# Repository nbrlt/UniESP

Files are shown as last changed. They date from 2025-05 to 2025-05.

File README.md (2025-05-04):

# UniESP
This is a simple board to control 2 unipolar stepper motors. It is meant to control a telescope mount using OnStepX on the ESP32. 

It relies on an ESP32 dev board with 30 pins and a RP2040 in the form of the Raspberry pico zero from waveshare as the driver logic. 

The code for OnStepX is found here: https://github.com/nbrlt/OnStepX (for now).
## The RP2040
The RP2040 is used to convert the StepDir interface of OnStepX to a 4 pin control for the DRV8932. I used that specific bridge driver to have a current control on the stepper (I could not find any StepDir bridge with proper current control).

The code for the Raspberry pico zero can be found here: [https://github.com/nbrlt/RP2040_Unipolar_StepDir_Driver](https://github.com/nbrlt/RP2040_StepDirToPWM_StepperLogic)

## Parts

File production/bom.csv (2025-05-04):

Designator | Footprint | Quantity | Value | LCSC Part #
C1, C16, C17 | 0402 | 3 | 0.01uF
C10, C4 | CP_Radial_D6.3mm_P2.50mm | 2 | 100uF
C11, C5 | 0402 | 2 | 0.022uF
C12, C15, C6, C9 | 0402 | 4 | 0.01uF
C13, C7 | 0603 | 2 | 0.22uF
C14, C8 | 0603 | 2 | 0.47uF
C2 | 0603 | 1 | 10uF
C3 | CP_Radial_D6.3mm_P2.50mm | 1 | 220uF
D1 | D_SMA | 1 | D | C14996
J1 | PinHeader_1x04_P2.54mm_Vertical | 1 | Power Conn
J2 | JST_NV_B02P-NV_1x02_P5.00mm_Vertical | 1 | 12V Input
J3 | PinHeader_1x05_P2.54mm_Vertical | 1 | RTC conn
J4 | PinSocket_1x10_P2.54mm_Vertical | 1 | Extra conn
J5 | JST_XH_B5B-XH-A_1x05_P2.50mm_Vertical | 1 | Motor2_Output
J6 | RJ45_HALO_HFJ11-x2450HRL_Horizontal | 1 | M2_out
J7 | JST_XH_B5B-XH-A_1x05_P2.50mm_Vertical | 1 | Motor1_Output
J8 | RJ45_HALO_HFJ11-x2450HRL_Horizontal | 1 | M1_out
L1 | L_Changjiang_FNR5040S | 1 | 15uH | C167969
R1 | 0603 | 1 | 10k
R10, R4 | 0603 | 2 | 330k
R11, R5 | 0603 | 2 | 3k
R12, R6 | 0603 | 2 | 4.7k
R13, R7 | 0603 | 2 | 10k
R14, R8 | 0603 | 2 | 27k
R15, R16, R3, R9 | 0603 | 4 | 47k
R2 | 0603 | 1 | 3.3k
RP2040_ZERO1 | WS_Pico_Zero_header | 1 | ~
U1 | TI_SO-PowerPAD-8_ThermalVias | 1 | TPS5430DDA | C9864
U2 | ESP32-DevKitV1 | 1 | ESP32-DevKitV1
U3, U4 | VQFN-24-1EP_4x4mm_P0.5mm_EP2.45x2.45mm_BIGThermalVias | 2 | DRV8932 | C2876703

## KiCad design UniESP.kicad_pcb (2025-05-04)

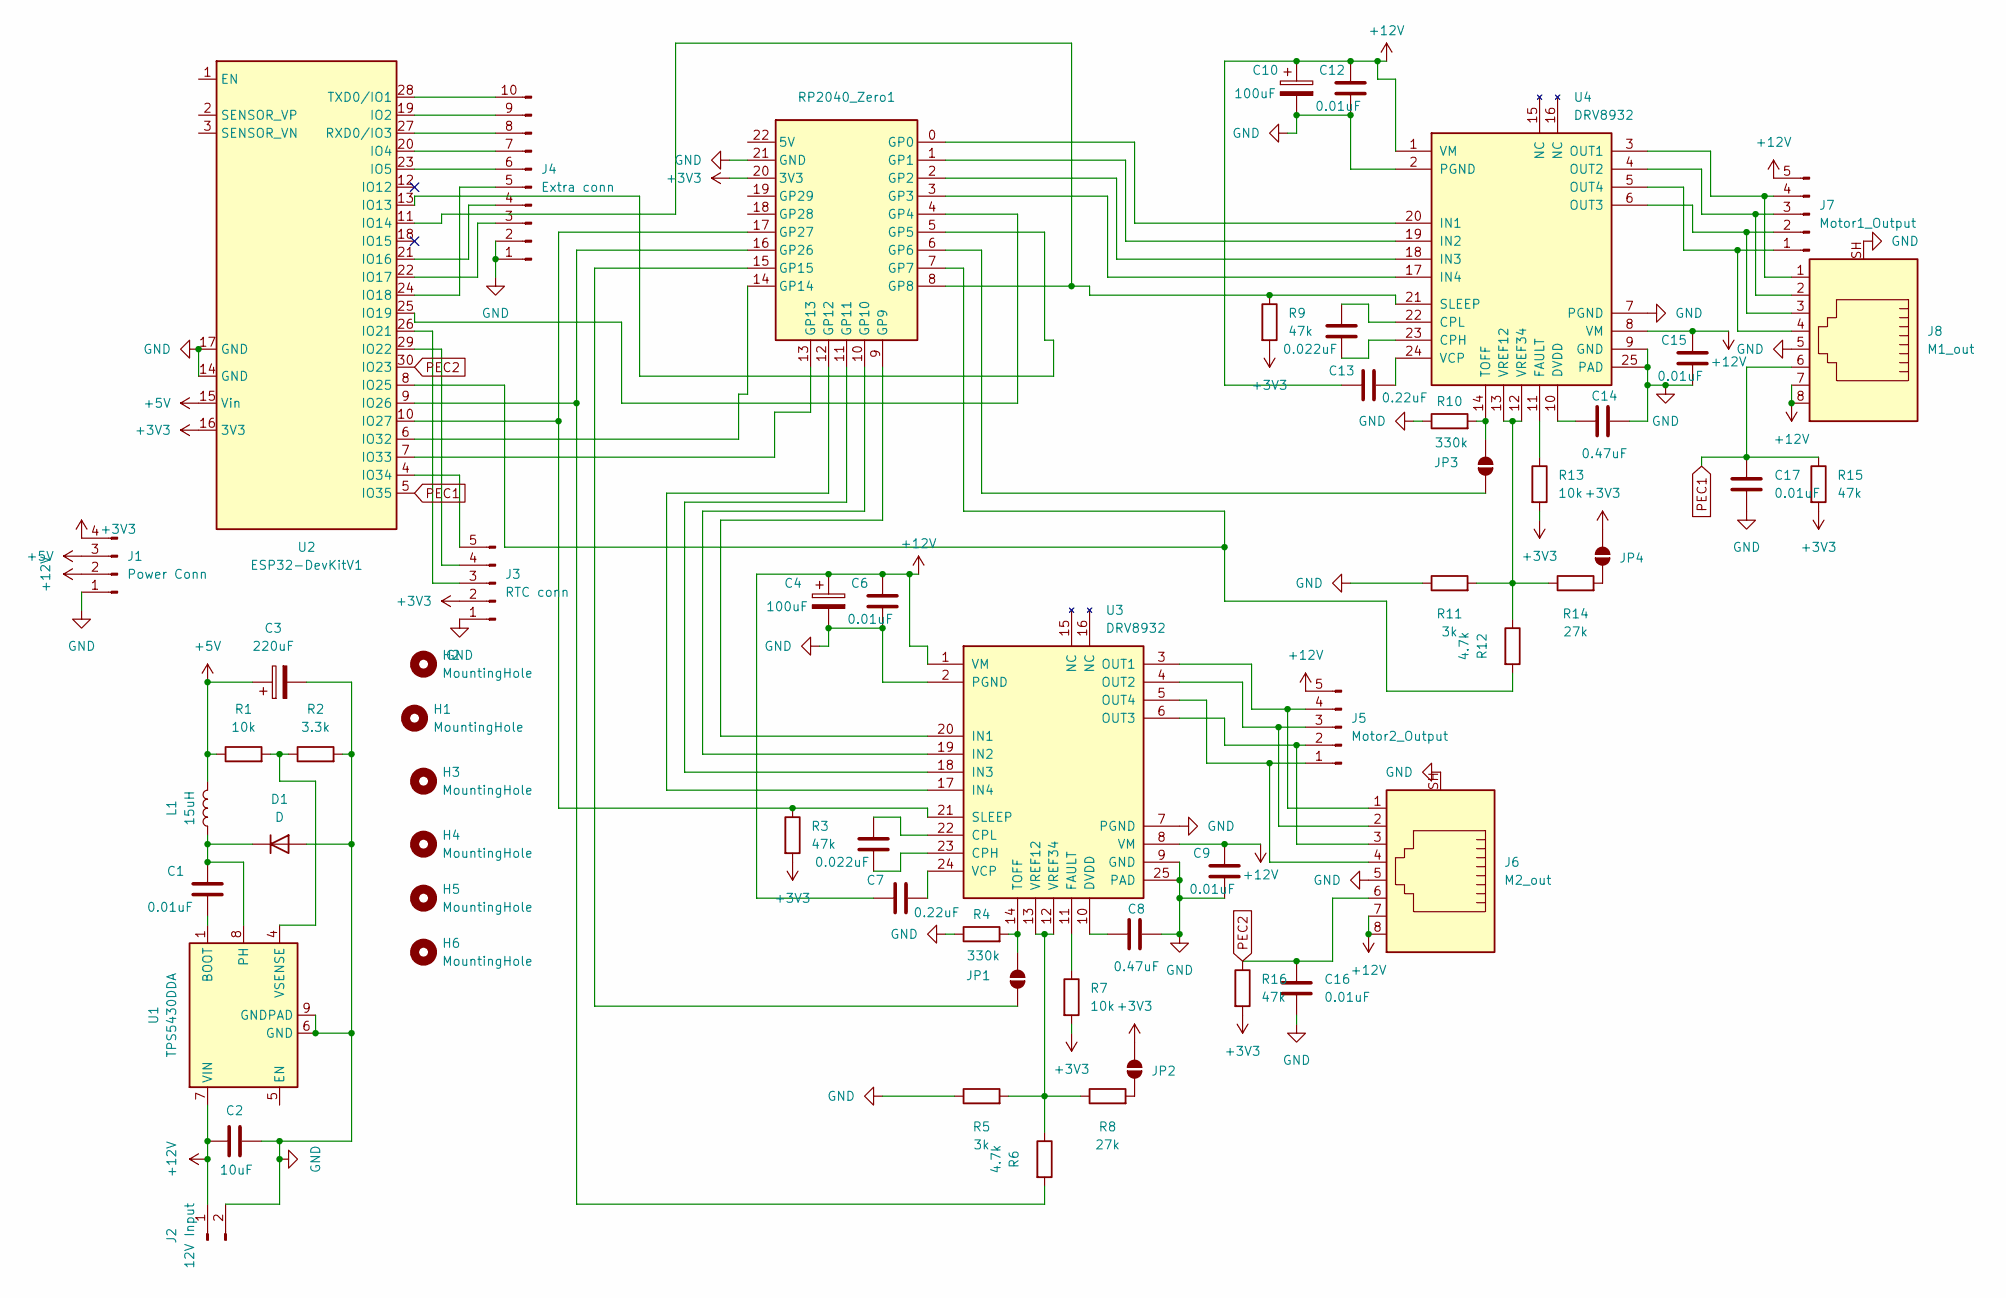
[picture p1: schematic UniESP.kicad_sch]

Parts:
C1, C6, C9, C12, C15, C16, C17: 0.01uF; C_0402_1005Metric
C2: 10uF; C_0603_1608Metric
C3: 220uF; CP_Radial_D6.3mm_P2.50mm
C4, C10: 100uF; CP_Radial_D6.3mm_P2.50mm
C5, C11: 0.022uF; C_0402_1005Metric
C7, C13: 0.22uF; C_0603_1608Metric
C8, C14: 0.47uF; C_0603_1608Metric
D1: D; D_SMA; LCSC C14996
H1, H2, H3, H6: MountingHole; JLCPCB_MountingHole
H4, H5: MountingHole; MountingHole_2.2mm_M2
J1: Power Conn; PinHeader_1x04_P2.54mm_Vertical
J2: 12V Input; JST_NV_B02P-NV_1x02_P5.00mm_Vertical
J3: RTC conn; PinHeader_1x05_P2.54mm_Vertical
J4: Extra conn; PinSocket_1x10_P2.54mm_Vertical
J5: Motor2_Output; JST_XH_B5B-XH-A_1x05_P2.50mm_Vertical
J6: M2_out; RJ45_HALO_HFJ11-x2450HRL_Horizontal
J7: Motor1_Output; JST_XH_B5B-XH-A_1x05_P2.50mm_Vertical
J8: M1_out; RJ45_HALO_HFJ11-x2450HRL_Horizontal
JP1: M2_Toff_MCU; SolderJumper-2_P1.3mm_Open_TrianglePad1.0x1.5mm
JP2: M2_Vref_5V; SolderJumper-2_P1.3mm_Open_TrianglePad1.0x1.5mm
JP3: M1_Toff_MCU; SolderJumper-2_P1.3mm_Open_TrianglePad1.0x1.5mm
JP4: M1_Vref_5V; SolderJumper-2_P1.3mm_Open_TrianglePad1.0x1.5mm
L1: 15uH; L_Changjiang_FNR5040S; LCSC C167969
R1, R7, R13: 10k; R_0603_1608Metric
R2: 3.3k; R_0603_1608Metric
R3, R9, R15, R16: 47k; R_0603_1608Metric
R4, R10: 330k; R_0603_1608Metric
R5, R11: 3k; R_0603_1608Metric
R6, R12: 4.7k; R_0603_1608Metric
R8, R14: 27k; R_0603_1608Metric
RP2040_Zero1: WS_Pico_Zero_header
U1: TPS5430DDA; TI_SO-PowerPAD-8_ThermalVias; LCSC C9864
U2: ESP32-DevKitV1
U3, U4: DRV8932; VQFN-24-1EP_4x4mm_P0.5mm_EP2.45x2.45mm_BIGThermalVias; LCSC C2876703

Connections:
+3V3: J1.4, J3.2, JP2.2 (B), JP4.2 (B), R3.2, R7.2, R9.2, R13.2, R15.2, R16.2, RP2040_Zero1.20 (3V3), U2.16 (3V3)
+5V: C3.1, J1.3, L1.2, R1.1, U2.15 (Vin)
+12V: C2.1, C4.1, C6.1, C7.2, C9.1, C10.1, C12.1, C13.2, C15.1, J1.2, J2.1, J5.5, J6.7, J6.8, J7.5, J8.7, J8.8, U1.7 (VIN), U3.1 (VM), U3.8 (VM), U4.1 (VM), U4.8 (VM)
GND: C2.2, C3.2, C4.2, C6.2, C8.2, C9.2, C10.2, C12.2, C14.2, C15.2, C16.2, C17.2, D1.2 (A), J1.1, J2.2, J3.1, J4.1, J4.2, J6.5, J6.SH, J8.5, J8.SH, R2.2, R4.1, R5.1, R10.1, R11.1, RP2040_Zero1.21 (GND), U1.6 (GND), U1.9 (GNDPAD), U2.14 (GND), U2.17 (GND), U3.2 (PGND), U3.7 (PGND), U3.9 (GND), U3.25 (PAD), U4.2 (PGND), U4.7 (PGND), U4.9 (GND), U4.25 (PAD)
unnamed: C1.1, D1.1 (K), L1.1, U1.8 (PH)
unnamed: J3.3, U2.26 (IO21)
unnamed: J3.4, U2.29 (IO22)
unnamed: J3.5, U2.4 (IO34)
unnamed: J4.3, U2.22 (IO17)
unnamed: J4.4, U2.21 (IO16)
unnamed: J4.5, U2.24 (IO18)
unnamed: J4.6, U2.23 (IO5)
unnamed: J4.7, U2.20 (IO4)
unnamed: J4.8, U2.27 (RXD0/IO3)
unnamed: J4.9, U2.19 (IO2)
unnamed: J4.10, U2.28 (TXD0/IO1)
unnamed: J5.1, J6.4, U3.5 (OUT4)
unnamed: J5.2, J6.3, U3.6 (OUT3)
unnamed: J5.3, J6.2, U3.4 (OUT2)
unnamed: J5.4, J6.1, U3.3 (OUT1)
unnamed: J7.1, J8.4, U4.5 (OUT4)
unnamed: J7.2, J8.3, U4.6 (OUT3)
unnamed: J7.3, J8.2, U4.4 (OUT2)
unnamed: J7.4, J8.1, U4.3 (OUT1)
unnamed: JP1.1 (A), RP2040_Zero1.15 (GP15)
unnamed: JP1.2 (B), R4.2, U3.14 (TOFF)
unnamed: JP2.1 (A), R8.2
unnamed: JP3.1 (A), RP2040_Zero1.6 (GP6)
unnamed: JP3.2 (B), R10.2, U4.14 (TOFF)
unnamed: JP4.1 (A), R14.2
unnamed: RP2040_Zero1.0 (GP0), U4.20 (IN1)
unnamed: RP2040_Zero1.1 (GP1), U4.19 (IN2)
unnamed: RP2040_Zero1.2 (GP2), U4.18 (IN3)
unnamed: RP2040_Zero1.3 (GP3), U4.17 (IN4)
unnamed: RP2040_Zero1.4 (GP4), U2.25 (IO19)
unnamed: RP2040_Zero1.5 (GP5), U2.13 (IO13)
unnamed: R12.2, RP2040_Zero1.7 (GP7), U2.8 (IO25)
unnamed: R9.1, RP2040_Zero1.8 (GP8), U2.11 (IO14), U4.21 (SLEEP)
unnamed: RP2040_Zero1.9 (GP9), U3.20 (IN1)
unnamed: RP2040_Zero1.10 (GP10), U3.19 (IN2)
unnamed: RP2040_Zero1.11 (GP11), U3.18 (IN3)
unnamed: RP2040_Zero1.12 (GP12), U3.17 (IN4)
unnamed: RP2040_Zero1.13 (GP13), U2.7 (IO33)
unnamed: RP2040_Zero1.14 (GP14), U2.6 (IO32)
unnamed: R6.2, RP2040_Zero1.16 (GP26), U2.9 (IO26)
unnamed: R3.1, RP2040_Zero1.17 (GP27), U2.10 (IO27), U3.21 (SLEEP)
unnamed: C1.2, U1.1 (BOOT)
unnamed: R1.2, R2.1, U1.4 (VSENSE)
unnamed: C5.2, U3.23 (CPH)
unnamed: C5.1, U3.22 (CPL)
unnamed: C8.1, U3.10 (DVDD)
unnamed: R7.1, U3.11 (FAULT)
unnamed: C7.1, U3.24 (VCP)
unnamed: R5.2, R6.1, R8.1, U3.12 (VREF34), U3.13 (VREF12)
unnamed: C11.2, U4.23 (CPH)
unnamed: C11.1, U4.22 (CPL)
unnamed: C14.1, U4.10 (DVDD)
unnamed: R13.1, U4.11 (FAULT)
unnamed: C13.1, U4.24 (VCP)
unnamed: R11.2, R12.1, R14.1, U4.12 (VREF34), U4.13 (VREF12)
PEC1: C17.1, J8.6, R15.1, U2.5 (IO35)
PEC2: C16.1, J6.6, R16.1, U2.30 (IO23)

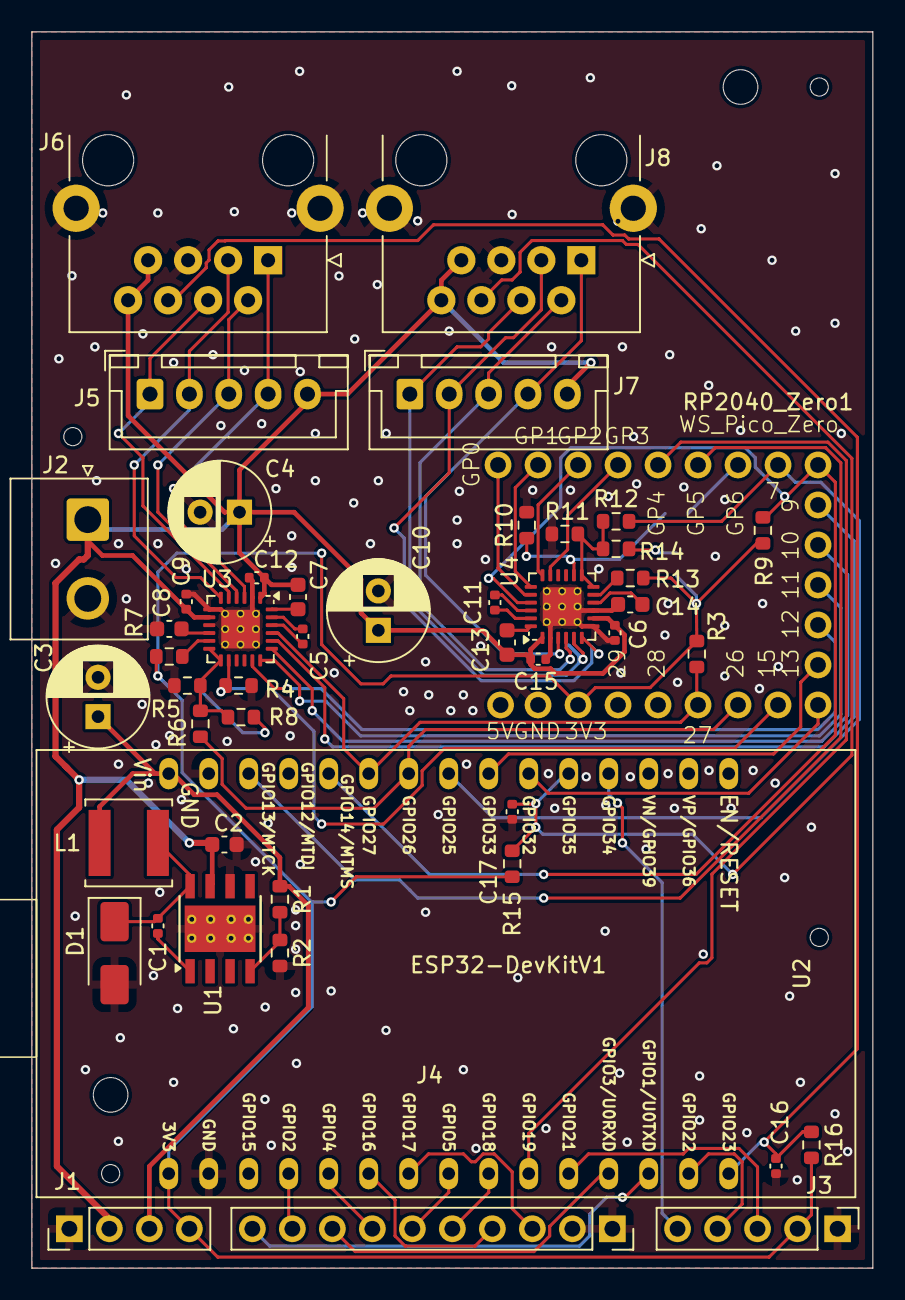
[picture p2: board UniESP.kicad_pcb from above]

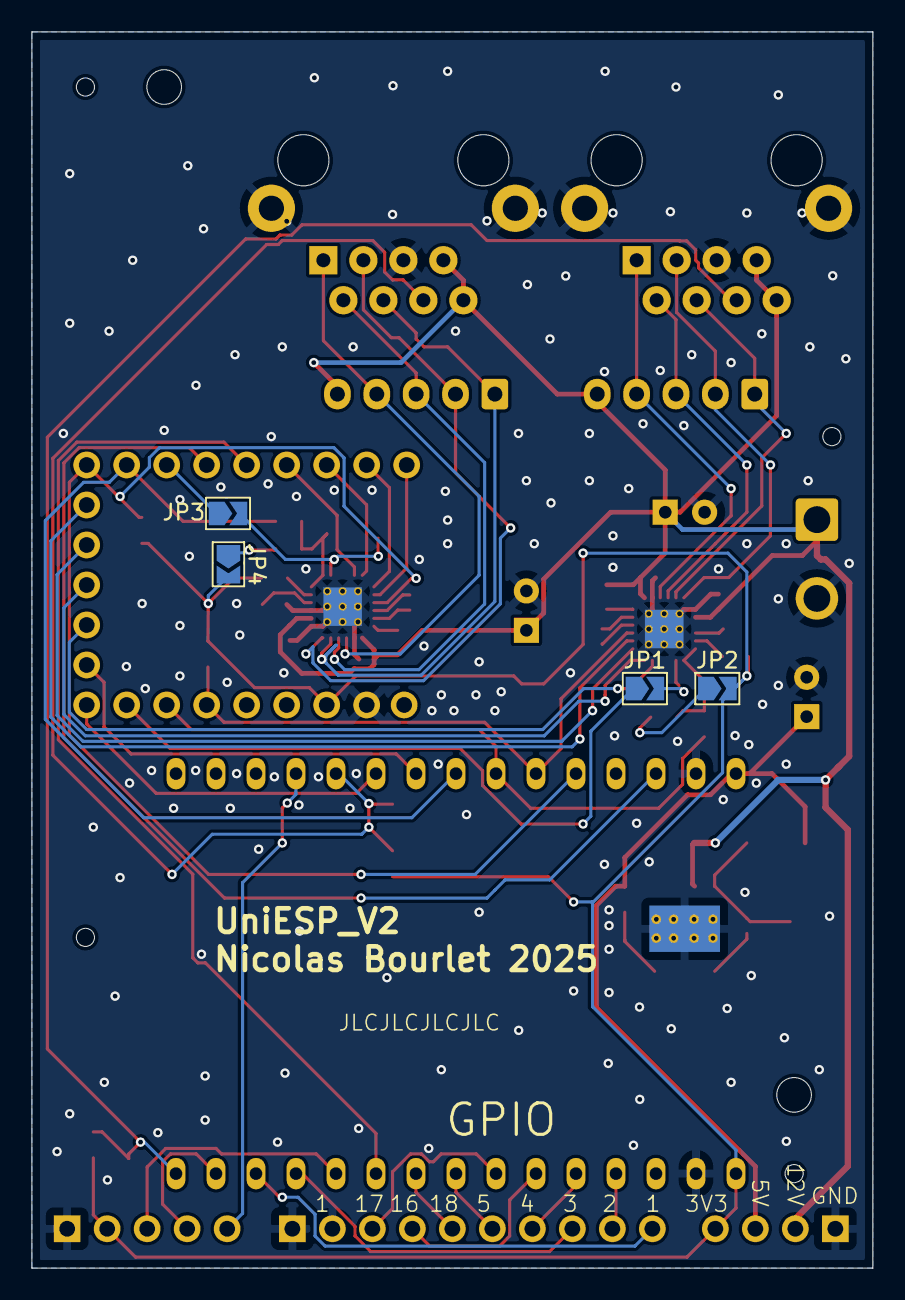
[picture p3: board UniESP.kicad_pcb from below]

Board: 2 copper layers, 53.4 x 78.5 mm, 58 parts (4 on the bottom side), 62 nets.
